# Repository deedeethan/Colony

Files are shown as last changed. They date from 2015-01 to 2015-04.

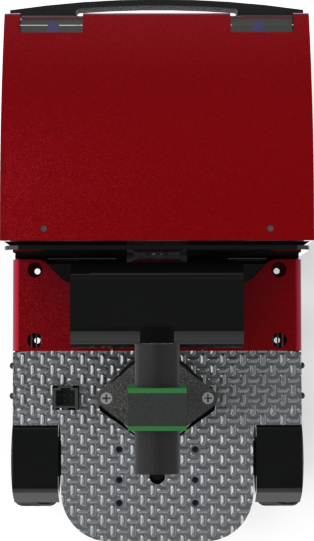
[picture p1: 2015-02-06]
high-level/catkin/misty_working/scoutsim/images/scout_large.png

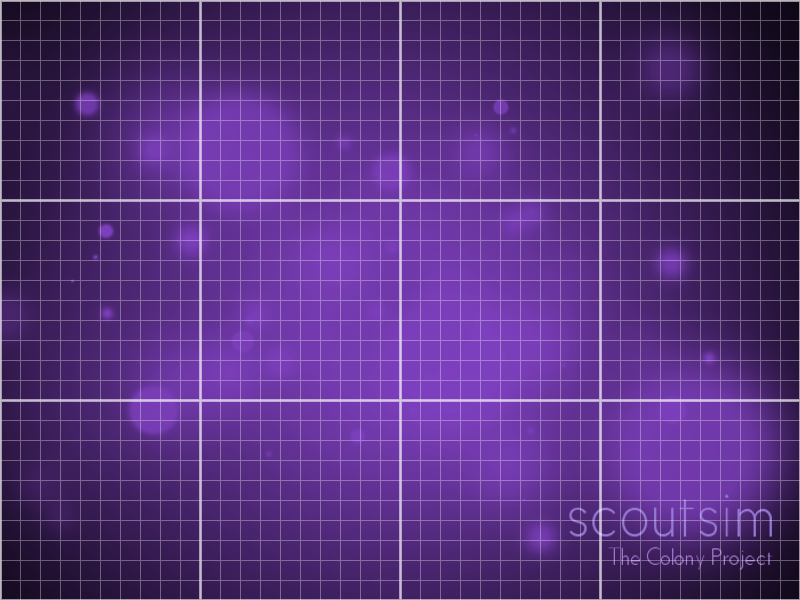
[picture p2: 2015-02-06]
high-level/catkin/misty_working/scoutsim/maps/grid.bmp

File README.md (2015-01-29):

Colony
======

Colony Scout

**General Body Meeting: Thursdays at 5:30pm in WEH 5312**
- Mechanical: Saturdays 1pm in Roboclub
  - contact Jason Dynes (jdynes@andrew.cmu.edu)
- Electrical: Saturdays 1pm in Roboclub
  - contact Jess Chernak (jchernak@andrew.cmu.edu)
- Low Level: Saturdays 3:30pm in Roboclub
  - contact Tom Mullins (tmullins@andrew.cmu.edu)
- High Level: Thursdays after GBM (6:00pm) in WEH 5312
  - contact Tim Brown (twbrown@andrew.cmu.edu)

Contact: [aperley@andrew.cmu.edu](mailto:aperley@andrew.cmu.edu), [jchernak@andrew.cmu.edu](mailto:jchernak@andrew.cmu.edu)

[Wiki](https://github.com/CMU-Robotics-Club/Colony/wiki)
--------------------------------------------------------

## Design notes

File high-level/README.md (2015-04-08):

TODO:
* Catkinize simulator
* Catkinize library/behaviors
* Debug Odometry_new
* Add more colors for each new scout in the simulator
* Remove old track lines when you kill a scout

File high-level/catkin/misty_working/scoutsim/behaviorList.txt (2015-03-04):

pause_scout
danger_marking
draw_ccw_circle
draw_cw_circle
line_follow
maze_solve
maze_solve_simple
navigationMap
Odometry
Odometry_new
Scheduler
smart_runaround
WH_Robot
wl_test

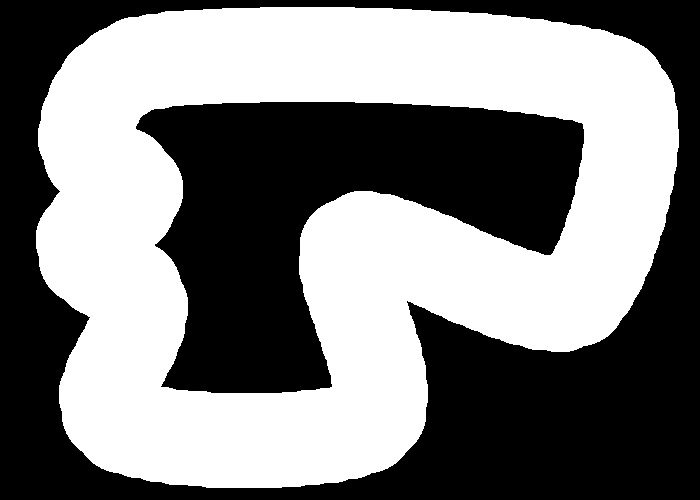
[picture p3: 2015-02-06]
high-level/catkin/misty_working/scoutsim/maps/race_walls.bmp

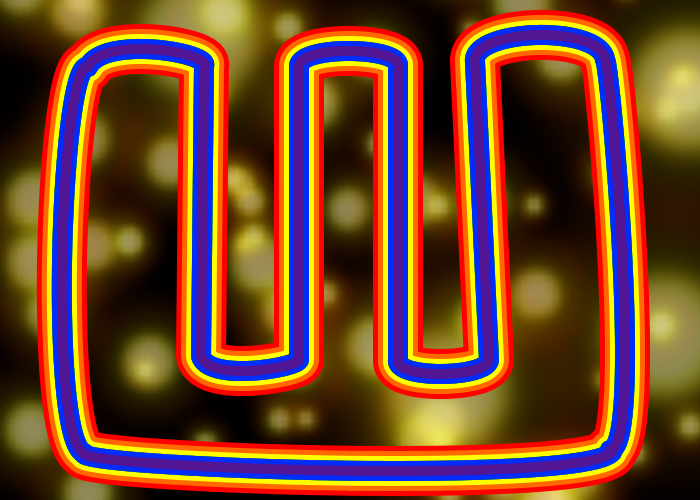
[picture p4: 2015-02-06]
high-level/catkin/misty_working/scoutsim/maps/line_follow3.bmp

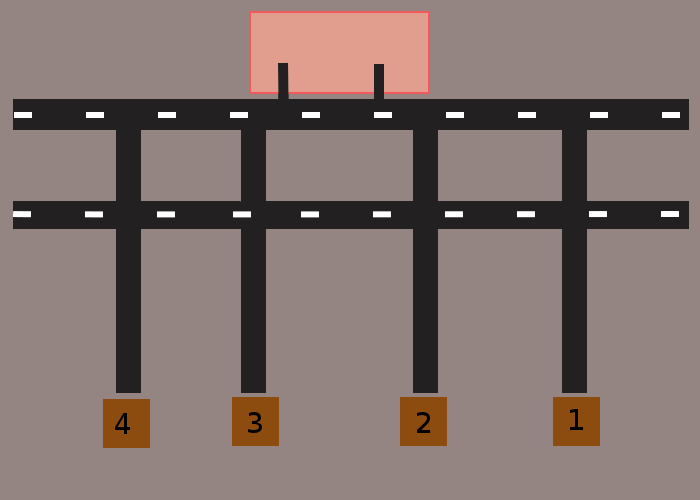
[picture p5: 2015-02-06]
high-level/catkin/misty_working/scoutsim/maps/warehouse.bmp

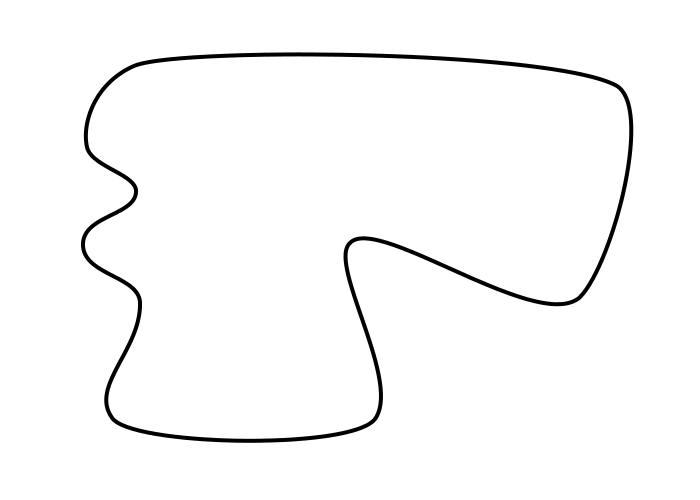
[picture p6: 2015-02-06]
high-level/catkin/misty_working/scoutsim/maps/racetest_lines.bmp

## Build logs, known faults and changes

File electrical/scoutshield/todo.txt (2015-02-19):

ScoutShield
==

- motor controllers
- stepper driver
- IMU
  - accel (MMA8452Q)
  - gyro (L3G4200D)
  - magnometer (MAG3110)
- rgb leds
  - puddle lights
- buttons
  - reset
  - user
  - power switch
- power connector
  - reverse protection
  - fuse
- power indicators
- connectors

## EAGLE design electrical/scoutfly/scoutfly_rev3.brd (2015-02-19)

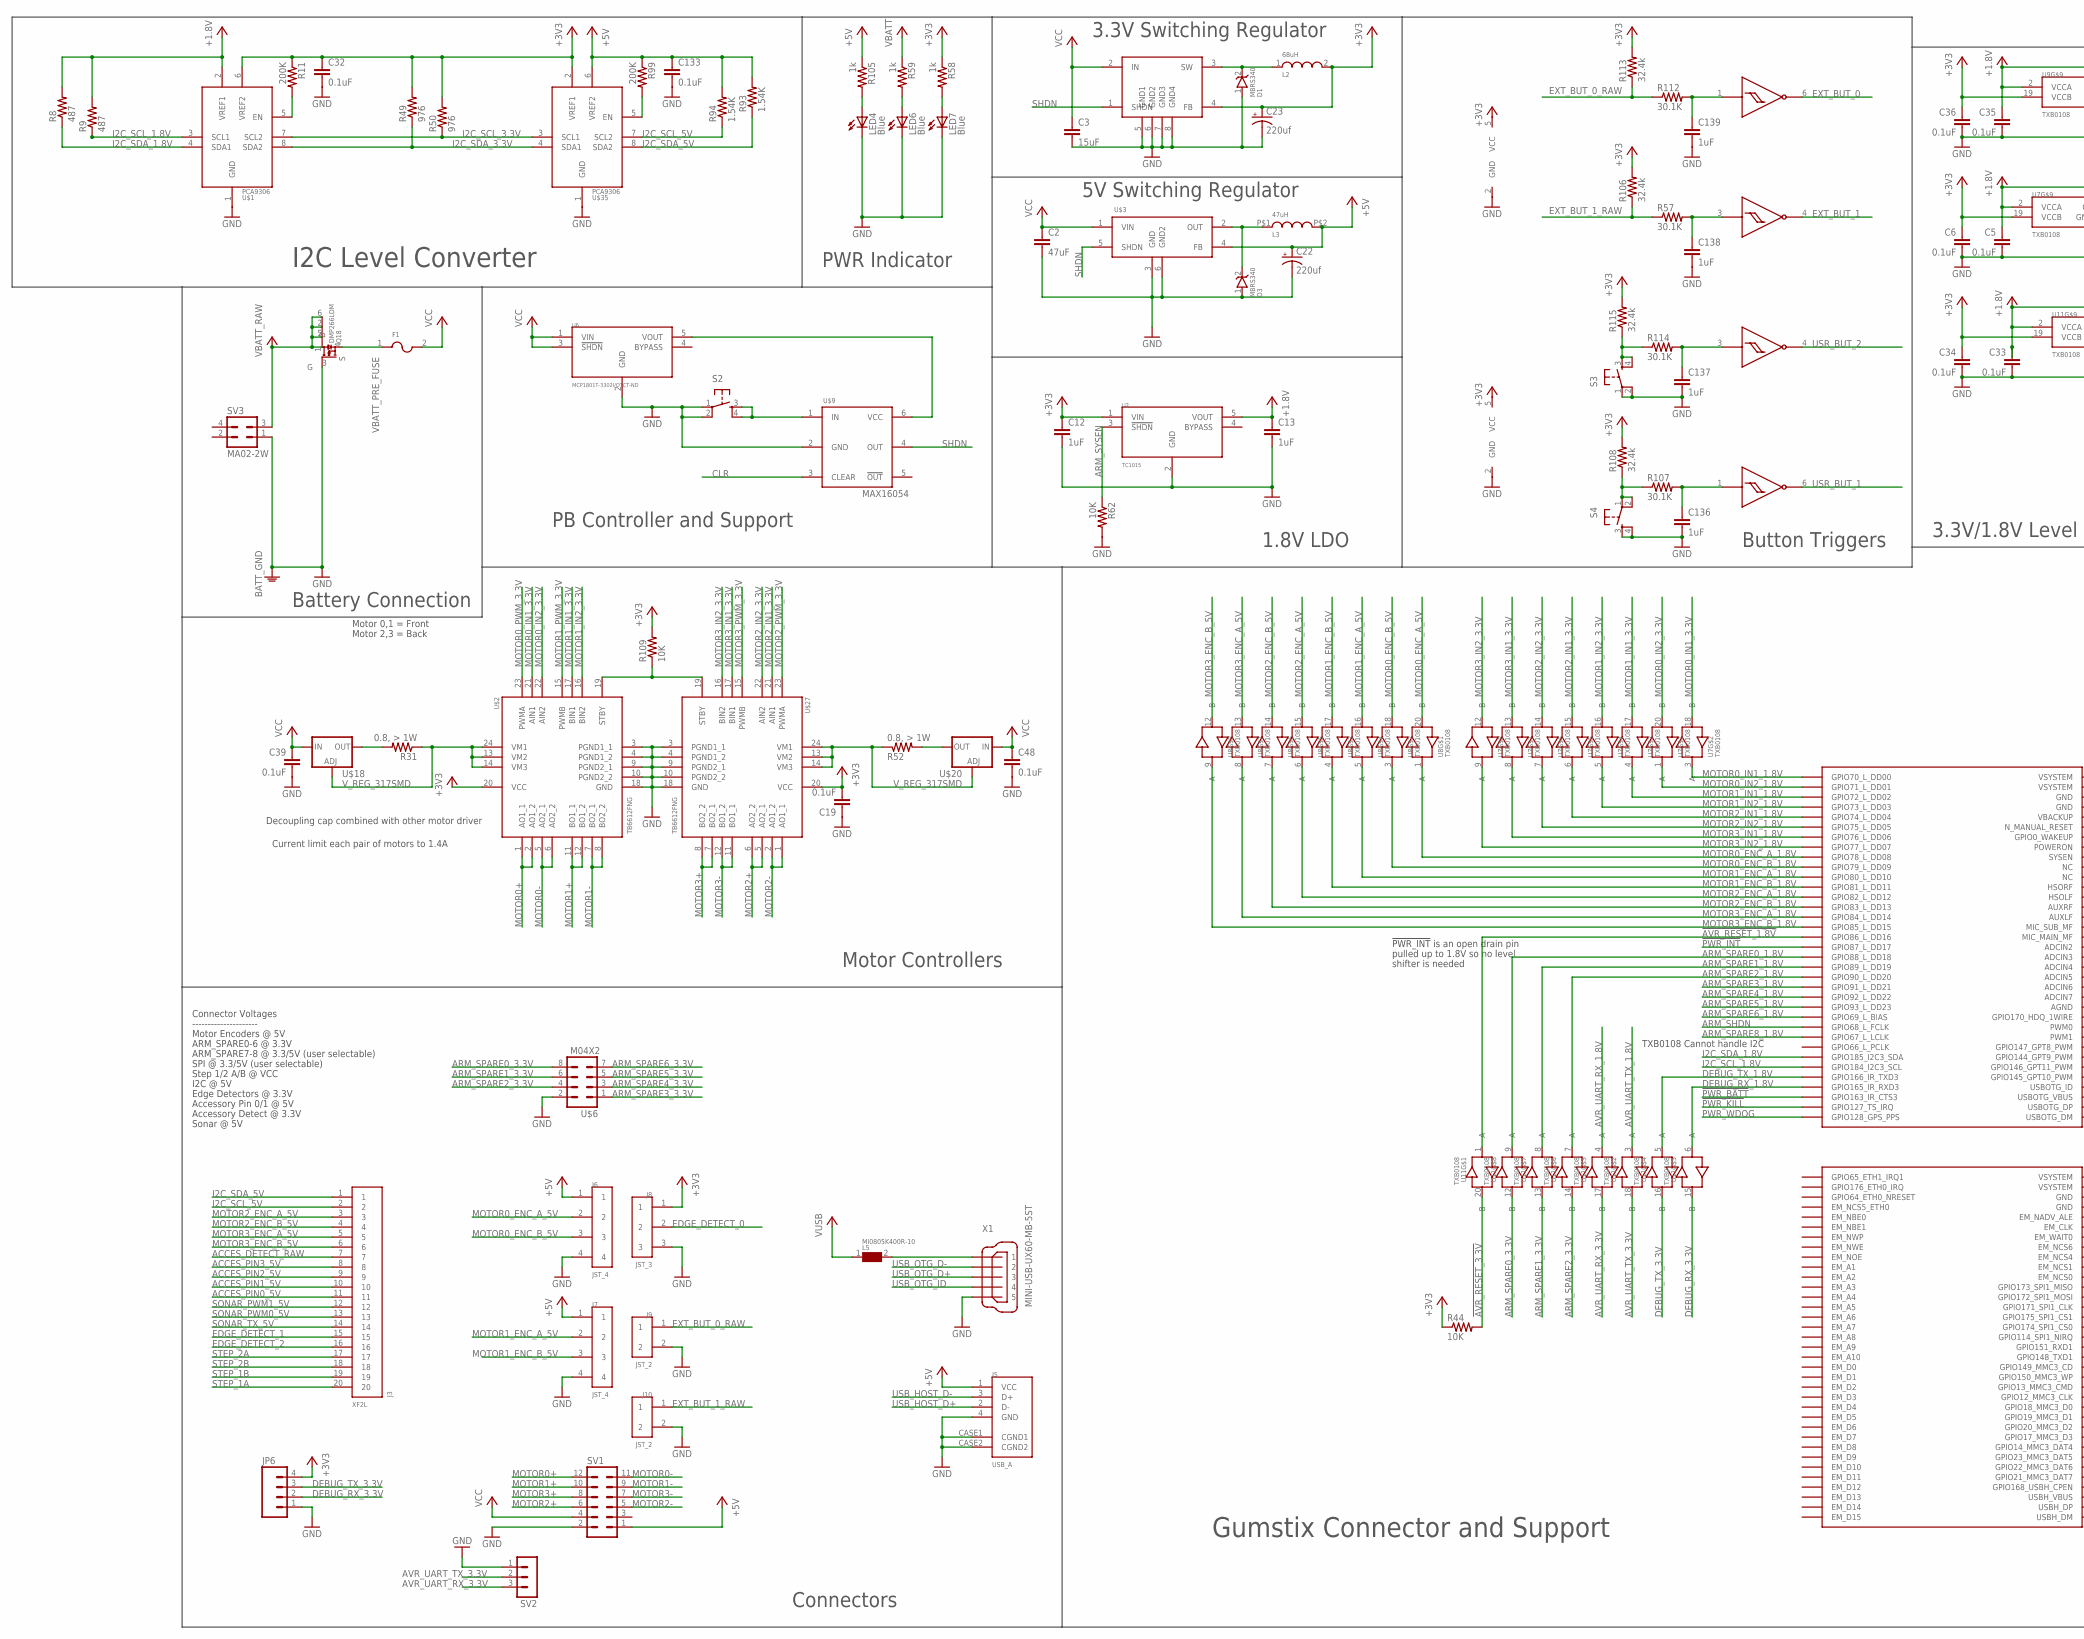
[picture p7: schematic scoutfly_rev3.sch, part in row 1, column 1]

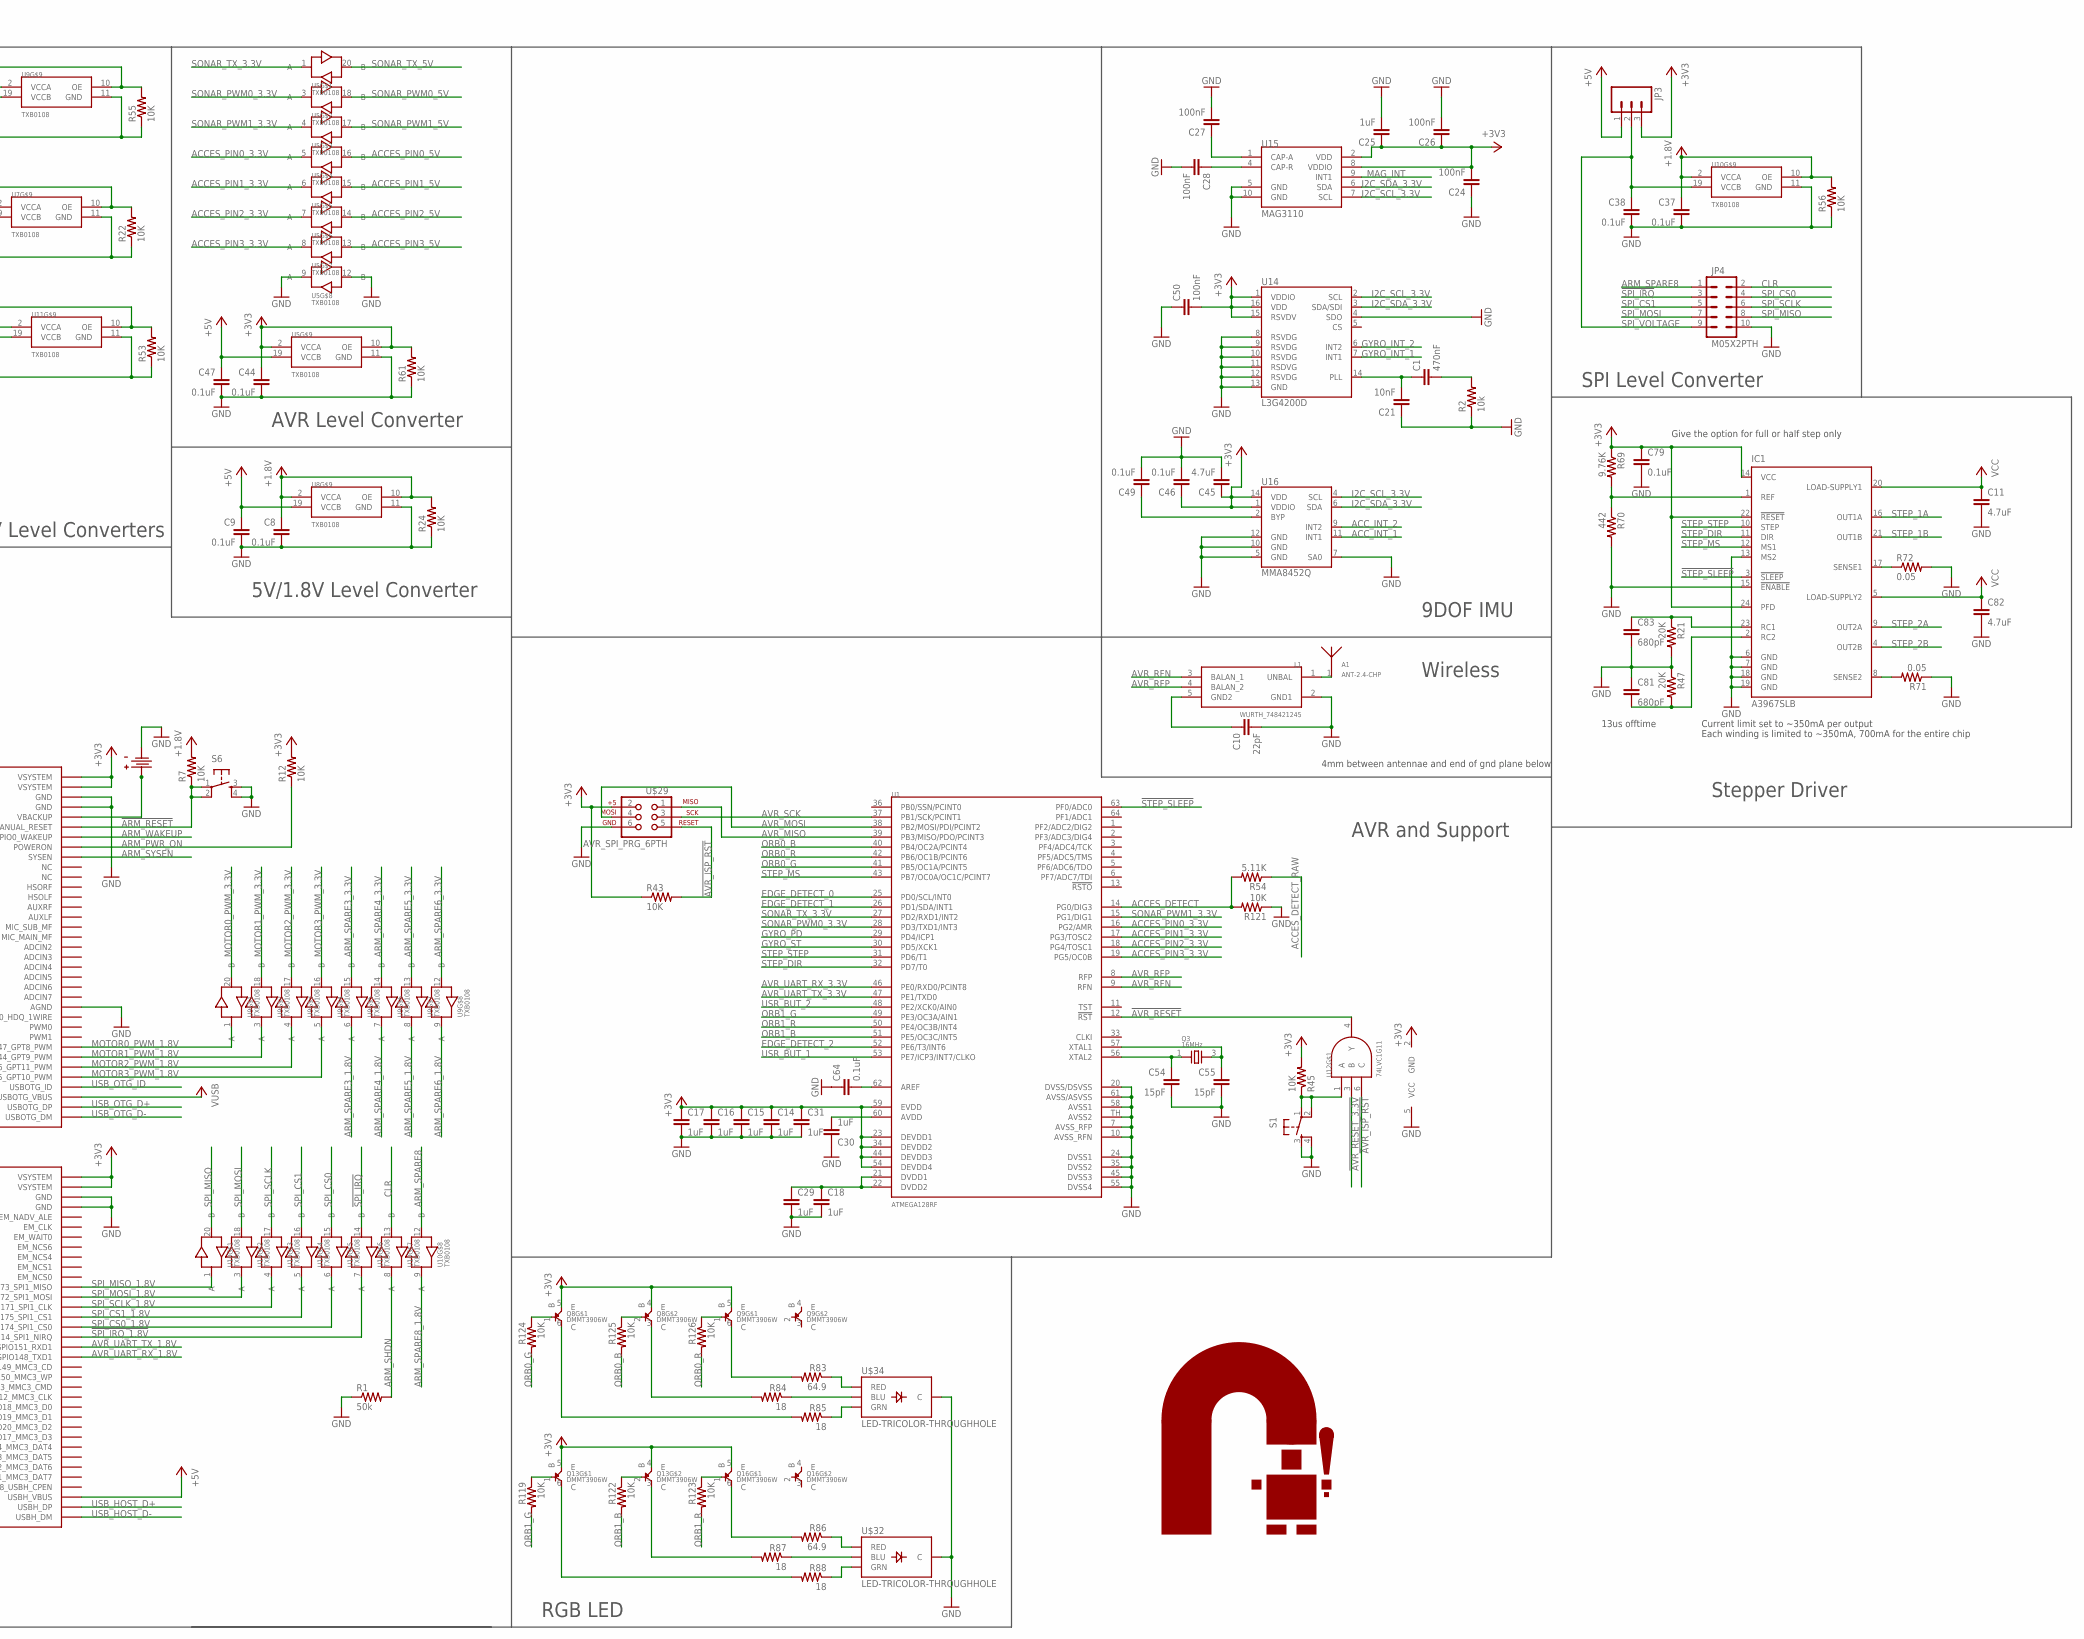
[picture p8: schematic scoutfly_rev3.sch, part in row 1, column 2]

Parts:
A1: ANT-2.4-CHP; CHIP_ANT_2.4GHZ
C1: 470nF; 0603-CAP
C2: 47uF; 0805
C3: 15uF; 0603-CAP
C5, C6, C8, C9, C19, C32, C33, C34, C35, C36, C37, C38, C39, C44, C46, C47, C48, C49, C64, C79, C133: 0.1uF; 0603-CAP
C10: 22pF; 0603-CAP
C11, C82: 4.7uF; C0805
C12, C13, C14, C15, C16, C17, C18, C25, C29, C30, C31, C136, C137, C138, C139: 1uF; 0603-CAP
C21: 10nF; 0603-CAP
C22, C23: 220uf; CT6032
C24, C26, C27, C28, C50: 100nF; 0603-CAP
C45: 4.7uF; 0603-CAP
C54, C55: 15pF; 0603-CAP
C81, C83: 680pF; 0603-CAP
D1, D3: MBRS340; SMC/DO-214AB
F1: MF-SM200; SM200
IC1: A3967SLB; SO24W
J3: XF2L; OMRON_XF
J5: USB_A
J6, J7: JST_4; JST_ZH_4
J8: JST_3; JST_ZH_3
J9, J10: JST_2; JST_ZH_2
J12: KEYSTONE_3000; COIN_CELL
JP3: M03PTH; 1X03
JP4: M05X2PTH; AVR_ICSP
JP6: M04LOCK; 1X04_LOCK
L1: WURTH_748421245; WURTH_BALUN
L2: 68uH; NR6045
L3: 47uH; 0.492L0.492W0.236HINDUCTOR
L5: MI0805K400R-10; 0805
LED4, LED6, LED7: Blue; LED-0603
Q3: 16MHz; NX3225SA
Q8, Q9, Q13, Q16: DMMT3906W; SOT363
Q18: DMP266LDM; SOT26
R1: 50k; R0603
R2: 10k; R0603
R7, R12, R22, R24, R43, R44, R45, R53, R55, R56, R61, R62, R109, R119, R121, R122, R123, R124, R125, R126: 10K; R0603
R8, R9: 487; R0603
R11, R99: 200K; R0603
R21, R47: 20K; R0603
R31, R52: 0.8, > 1W; R2512
R49, R50: 976; R0603
R54: 5.11K; R0603
R57, R107, R112, R114: 30.1K; R0603
R58, R59, R105: 1k; R0603
R69: 9.76K; R0603
R70: 442; R0603
R71, R72: 0.05; R0603
R83, R86: 64.9; R0603
R84, R85, R87, R88: 18; R0603
R93, R94: 1.54K; R0603
R106, R108, R113, R115: 32.4k; R0603
S1, S2, S3, S4, S6: TAC_SWITCHSMD; TACTILE_SWITCH_SMD
SV1: MA06-2W
SV2: MA03-1
SV3: MA02-2W
U1: ATMEGA128RF; MLF64-TH
U2: TC1015; 5-SOT23
U3, U4: NL27WZ14; SOT363
U5, U7, U8, U9, U10, U11: TXB0108; 20-TSSOP
U6: MCP1801T-3302I/OTCT-ND; 5-SOT23
U12: 74LVC1G11; 6-SOT23
U14: L3G4200D; LGA16-4X4
U15: MAG3110; DFN-10
U16: MMA8452Q; QFN-16_0.5MM
U$1, U$35: PCA9306; TSSOP8
U$2, U$27: TB6612FNG; 24-SSOP
U$3: AP1501; DD2PAK
U$6: M04X2; 2X4
U$7: ROBOLOGOSILKSCREEN; RCLOGO
U$9: MAX16054; 6-TSOT23
U$10: MIC4680-3.3YM; 8-SOIC
U$16: OVERO
U$18, U$20: V_REG_317SMD; SOT223
U$29: AVR_SPI_PRG_6PTH; 2X3
U$32, U$34: LED-TRICOLOR-THROUGHHOLE
X1: MINI-USB-UX60-MB-5ST; UX60-MB-5ST

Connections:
!ARM_RESET: R7.1, S6.1, S6.2, U$16.N_MANUAL_RESET
!AVR_ISP_RST: R43.2, U12.6 (C), U$29.5
!AVR_RESET: U1.12 (!RST), U12.4 (Y)
!AVR_RESET_1.8V: U11.1 (A), U$16.GPIO86_L_DD16
!AVR_RESET_3.3V: R44.2, U11.20 (B), U12.3 (B)
!PWR_BATT: U$16.GPIO163_IR_CTS3
!PWR_INT: U$16.GPIO87_L_DD17
!PWR_KILL: U$16.GPIO127_TS_IRQ
!SPI_IRQ: JP4.3, U10.14 (B)
!SPI_IRQ_1.8V: U10.7 (A), U$16.GPIO114_SPI1_NIRQ
!STEP_SLEEP: IC1.3 (!SLEEP), U1.63 (PF0/ADC0)
+1.8V: C5.1, C8.1, C13.1, C33.1, C35.1, C37.1, R7.2, R8.2, R9.2, R22.2, R24.2, R53.2, R55.2, R56.2, U2.5 (VOUT), U7.2 (VCCA), U7.10 (OE), U8.2 (VCCA), U8.10 (OE), U9.2 (VCCA), U9.10 (OE), U10.2 (VCCA), U10.10 (OE), U11.2 (VCCA), U11.10 (OE), U$1.2 (VREF1)
+3V3: C6.1, C12.1, C14.1, C15.1, C16.1, C17.1, C19.2, C23.+, C24.2, C25.1, C26.1, C31.1, C32.1, C34.1, C36.1, C44.1, C45.1, C46.1, C50.2, C79.1, IC1.14 (VCC), IC1.22 (!RESET), IC1.24 (PFD), J8.1, JP3.3, JP6.4, L2.2, Q8.4 (E), Q8.5 (E), Q9.5 (E), Q13.4 (E), Q13.5 (E), Q16.5 (E), R11.1, R12.2, R43.1, R44.1, R45.2, R49.2, R50.2, R58.1, R61.2, R69.1, R106.2, R108.2, R109.2, R113.2, R115.2, U1.23 (DEVDD1), U1.34 (DEVDD2), U1.44 (DEVDD3), U1.54 (DEVDD4), U1.59 (EVDD), U2.1 (VIN), U3.5 (VCC), U4.5 (VCC), U5.2 (VCCA), U5.10 (OE), U7.19 (VCCB), U9.19 (VCCB), U11.19 (VCCB), U12.2 (GND), U14.1 (VDDIO), U14.15 (RSVDV), U14.16 (VDD), U15.2 (VDD), U15.8 (VDDIO), U16.1 (VDDIO), U16.14 (VDD), U$1.6 (VREF2), U$2.20 (VCC), U$10.4 (FB), U$16.VSYSTEM@1 (VSYSTEM), U$16.VSYSTEM@2 (VSYSTEM), U$16.VSYSTEM@66 (VSYSTEM), U$16.VSYSTEM@67 (VSYSTEM), U$27.20 (VCC), U$29.2, U$35.2 (VREF1)
+5V: C9.1, C22.+, C47.1, C133.1, J5.1 (VCC), J6.1, J7.1, JP3.1, L3.P$2 (2), R93.2, R94.2, R99.1, R105.1, SV1.1, U5.19 (VCCB), U8.19 (VCCB), U$3.4 (FB), U$16.USBH_VBUS, U$35.6 (VREF2)
ACCES_DETECT: R54.2, R121.2, U1.14 (PG0/DIG3)
ACCES_DETECT_RAW: J3.7, R54.1
ACCES_PIN0_3.3V: U1.16 (PG2/AMR), U5.5 (A)
ACCES_PIN0_5V: J3.11, U5.16 (B)
ACCES_PIN1_3.3V: U1.17 (PG3/TOSC2), U5.6 (A)
ACCES_PIN1_5V: J3.10, U5.15 (B)
ACCES_PIN2_3.3V: U1.18 (PG4/TOSC1), U5.7 (A)
ACCES_PIN2_5V: J3.9, U5.14 (B)
ACCES_PIN3_3.3V: U1.19 (PG5/OC0B), U5.8 (A)
ACCES_PIN3_5V: J3.8, U5.13 (B)
ACC_INT_1: U16.11 (INT1)
ACC_INT_2: U16.9 (INT2)
ARM_PWR_ON: R12.1, U$16.POWERON
ARM_SHDN: R1.2, U10.8 (A), U$16.GPIO68_L_FCLK
ARM_SPARE0_1.8V: U11.9 (A), U$16.GPIO88_L_DD18
ARM_SPARE0_3.3V: U11.12 (B), U$6.8
ARM_SPARE1_1.8V: U11.8 (A), U$16.GPIO89_L_DD19
ARM_SPARE1_3.3V: U11.13 (B), U$6.6
ARM_SPARE2_1.8V: U11.7 (A), U$16.GPIO90_L_DD20
ARM_SPARE2_3.3V: U11.14 (B), U$6.4
ARM_SPARE3_1.8V: U9.6 (A), U$16.GPIO91_L_DD21
ARM_SPARE3_3.3V: U9.15 (B), U$6.1
ARM_SPARE4_1.8V: U9.7 (A), U$16.GPIO92_L_DD22
ARM_SPARE4_3.3V: U9.14 (B), U$6.3
ARM_SPARE5_1.8V: U9.8 (A), U$16.GPIO93_L_DD23
ARM_SPARE5_3.3V: U9.13 (B), U$6.5
ARM_SPARE6_1.8V: U9.9 (A), U$16.GPIO69_L_BIAS
ARM_SPARE6_3.3V: U9.12 (B), U$6.7
ARM_SPARE8: JP4.1, U10.12 (B)
ARM_SPARE8_1.8V: U10.9 (A), U$16.GPIO67_L_LCLK
ARM_SYSEN: R62.1, U2.3 (!SHDN), U$16.SYSEN
ARM_WAKEUP: U$16.GPIO0_WAKEUP
AVR_MISO: U1.39 (PB3/MISO/PDO/PCINT3), U$29.1
AVR_MOSI: U1.38 (PB2/MOSI/PDI/PCINT2), U$29.4
AVR_RFN: L1.3 (BALAN_1), U1.9 (RFN)
AVR_RFP: L1.4 (BALAN_2), U1.8 (RFP)
AVR_SCK: U1.37 (PB1/SCK/PCINT1), U$29.3
AVR_UART_RX_1.8V: U11.4 (A), U$16.GPIO148_TXD1
AVR_UART_RX_3.3V: SV2.3, U1.46 (PE0/RXD0/PCINT8), U11.17 (B)
AVR_UART_TX_1.8V: U11.3 (A), U$16.GPIO151_RXD1
AVR_UART_TX_3.3V: SV2.2, U1.47 (PE1/TXD0), U11.18 (B)
CLR: JP4.2, U10.13 (B), U$9.3 (CLEAR)
DEBUG_RX_1.8V: U11.6 (A), U$16.GPIO165_IR_RXD3
DEBUG_RX_3.3V: JP6.2, U11.15 (B)
DEBUG_TX_1.8V: U11.5 (A), U$16.GPIO166_IR_TXD3
DEBUG_TX_3.3V: JP6.3, U11.16 (B)
EDGE_DETECT_0: J8.2, U1.25 (PD0/SCL/INT0)
EDGE_DETECT_1: J3.15, U1.26 (PD1/SDA/INT1)
EDGE_DETECT_2: J3.16, U1.52 (PE6/T3/INT6)
EXT_BUT_0: U3.6 (Y)
EXT_BUT_0_RAW: J9.1, R112.1, R113.1
EXT_BUT_1: U3.4 (Y)
EXT_BUT_1_RAW: J10.1, R57.1, R106.1
GND: C2.2, C3.2, C5.2, C6.2, C8.2, C9.2, C10.2, C11.2, C12.2, C13.2, C14.2, C15.2, C16.2, C17.2, C18.2, C19.1, C21.1, C22.-, C23.-, C24.1, C25.2, C26.2, C27.2, C28.2, C29.2, C30.1, C31.2, C32.2, C33.2, C34.2, C35.2, C36.2, C37.2, C38.2, C39.2, C44.2, C45.2, C46.2, C47.2, C48.2, C49.2, C50.1, C54.2, C55.2, C64.1, C79.2, C81.1, C82.2, C83.2, C133.2, C136.2, C137.2, C138.2, C139.2, D1.1, D3.1, IC1.6 (GND), IC1.7 (GND), IC1.13 (MS2), IC1.15 (!ENABLE), IC1.18 (GND), IC1.19 (GND), J5.4 (GND), J5.CASE1 (CGND1), J5.CASE2 (CGND2), J6.4, J7.4, J8.3, J9.2, J10.2, J12.NEGATIVE (-), JP4.10, JP6.1, L1.2 (GND1), LED4.C, LED6.C, LED7.C, Q18.3 (G), R1.1, R2.1, R21.2, R22.1, R24.1, R47.1, R53.1, R55.1, R56.1, R61.1, R62.2, R70.2, R71.1, R72.2, R121.1, S1.3, S1.4, S2.1, S2.2, S3.1, S3.2, S4.3, S4.4, S6.3, S6.4, SV1.2, SV2.1, SV3.1, U1.7 (AVSS_RFP), U1.10 (AVSS_RFN), U1.20 (DVSS/DSVSS), U1.24 (DVSS1), U1.35 (DVSS2), U1.45 (DVSS3), U1.55 (DVSS4), U1.58 (AVSS1), U1.61 (AVSS/ASVSS), U1.TH (AVSS2), U2.2 (GND), U3.2 (GND), U4.2 (GND), U5.9 (A), U5.11 (GND), U5.12 (B), U6.2 (GND), U7.11 (GND), U8.11 (GND), U9.11 (GND), U10.11 (GND), U11.11 (GND), U12.5 (VCC), U14.4 (SDO), U14.8 (RSVDG), U14.9 (RSVDG), U14.10 (RSVDG), U14.11 (RSDVG), U14.12 (RSVDG), U14.13 (GND), U15.5 (GND), U15.10 (GND), U16.5 (GND), U16.7 (SA0), U16.10 (GND), U16.12 (GND), U$1.1 (GND), U$2.3 (PGND1_1), U$2.4 (PGND1_2), U$2.9 (PGND2_1), U$2.10 (PGND2_2), U$2.18 (GND), U$3.3 (GND), U$3.6 (GND2), U$6.2, U$9.2 (GND), U$10.5 (GND1), U$10.6 (GND2), U$10.7 (GND3), U$10.8 (GND4), U$16.AGND, U$16.GND, U$16.GND@33 (GND), U$16.GND@56 (GND), U$16.GND@70 (GND), U$27.3 (PGND1_1), U$27.4 (PGND1_2), U$27.9 (PGND2_1), U$27.10 (PGND2_2), U$27.18 (GND), U$29.6, U$32.GND (C), U$34.GND (C), U$35.1 (GND), X1.5
GYRO_INT_1: U14.7 (INT1)
GYRO_INT_2: U14.6 (INT2)
GYRO_PD: U1.29 (PD4/ICP1)
GYRO_ST: U1.30 (PD5/XCK1)
I2C_SCL_1.8V: R9.1, U$1.3 (SCL1), U$16.GPIO184_I2C3_SCL
I2C_SCL_3.3V: R50.1, U14.2 (SCL), U15.7 (SCL), U16.4 (SCL), U$1.7 (SCL2), U$35.3 (SCL1)
I2C_SCL_5V: J3.2, R94.1, U$35.7 (SCL2)
I2C_SDA_1.8V: R8.1, U$1.4 (SDA1), U$16.GPIO185_I2C3_SDA
I2C_SDA_3.3V: R49.1, U14.3 (SDA/SDI), U15.6 (SDA), U16.6 (SDA), U$1.8 (SDA2), U$35.4 (SDA1)
I2C_SDA_5V: J3.1, R93.1, U$35.8 (SDA2)
MAG_INT: U15.9 (INT1)
MOTOR0+: SV1.12, U$2.1 (AO1_1), U$2.2 (AO1_2)
MOTOR0-: SV1.11, U$2.5 (AO2_1), U$2.6 (AO2_2)
MOTOR0_ENC_A_1.8V: U8.1 (A), U$16.GPIO78_L_DD08
MOTOR0_ENC_A_5V: J6.2, U8.20 (B)
MOTOR0_ENC_B_1.8V: U8.3 (A), U$16.GPIO79_L_DD09
MOTOR0_ENC_B_5V: J6.3, U8.18 (B)
MOTOR0_IN1_1.8V: U7.3 (A), U$16.GPIO70_L_DD00
MOTOR0_IN1_3.3V: U7.18 (B), U$2.21 (AIN1)
MOTOR0_IN2_1.8V: U7.1 (A), U$16.GPIO71_L_DD01
MOTOR0_IN2_3.3V: U7.20 (B), U$2.22 (AIN2)
MOTOR0_PWM_1.8V: U9.1 (A), U$16.GPIO147_GPT8_PWM
MOTOR0_PWM_3.3V: U9.20 (B), U$2.23 (PWMA)
MOTOR1+: SV1.10, U$2.11 (BO1_1), U$2.12 (BO1_2)
MOTOR1-: SV1.9, U$2.7 (BO2_1), U$2.8 (BO2_2)
MOTOR1_ENC_A_1.8V: U8.5 (A), U$16.GPIO80_L_DD10
MOTOR1_ENC_A_5V: J7.2, U8.16 (B)
MOTOR1_ENC_B_1.8V: U8.4 (A), U$16.GPIO81_L_DD11
MOTOR1_ENC_B_5V: J7.3, U8.17 (B)
MOTOR1_IN1_1.8V: U7.4 (A), U$16.GPIO72_L_DD02
MOTOR1_IN1_3.3V: U7.17 (B), U$2.17 (BIN1)
MOTOR1_IN2_1.8V: U7.5 (A), U$16.GPIO73_L_DD03
MOTOR1_IN2_3.3V: U7.16 (B), U$2.16 (BIN2)
MOTOR1_PWM_1.8V: U9.3 (A), U$16.GPIO144_GPT9_PWM
MOTOR1_PWM_3.3V: U9.18 (B), U$2.15 (PWMB)
MOTOR2+: SV1.6, U$27.5 (AO2_1), U$27.6 (AO2_2)
MOTOR2-: SV1.5, U$27.1 (AO1_1), U$27.2 (AO1_2)
MOTOR2_ENC_A_1.8V: U8.6 (A), U$16.GPIO82_L_DD12
MOTOR2_ENC_A_5V: J3.3, U8.15 (B)
MOTOR2_ENC_B_1.8V: U8.7 (A), U$16.GPIO83_L_DD13
MOTOR2_ENC_B_5V: J3.4, U8.14 (B)
MOTOR2_IN1_1.8V: U7.6 (A), U$16.GPIO74_L_DD04
MOTOR2_IN1_3.3V: U7.15 (B), U$27.21 (AIN1)
MOTOR2_IN2_1.8V: U7.7 (A), U$16.GPIO75_L_DD05
MOTOR2_IN2_3.3V: U7.14 (B), U$27.22 (AIN2)
MOTOR2_PWM_1.8V: U9.4 (A), U$16.GPIO146_GPT11_PWM
MOTOR2_PWM_3.3V: U9.17 (B), U$27.23 (PWMA)
MOTOR3+: SV1.8, U$27.7 (BO2_1), U$27.8 (BO2_2)
MOTOR3-: SV1.7, U$27.11 (BO1_1), U$27.12 (BO1_2)
MOTOR3_ENC_A_1.8V: U8.8 (A), U$16.GPIO84_L_DD14
MOTOR3_ENC_A_5V: J3.5, U8.13 (B)
MOTOR3_ENC_B_1.8V: U8.9 (A), U$16.GPIO85_L_DD15
MOTOR3_ENC_B_5V: J3.6, U8.12 (B)
MOTOR3_IN1_1.8V: U7.8 (A), U$16.GPIO76_L_DD06
MOTOR3_IN1_3.3V: U7.13 (B), U$27.17 (BIN1)
MOTOR3_IN2_1.8V: U7.9 (A), U$16.GPIO77_L_DD07
MOTOR3_IN2_3.3V: U7.12 (B), U$27.16 (BIN2)
MOTOR3_PWM_1.8V: U9.5 (A), U$16.GPIO145_GPT10_PWM
MOTOR3_PWM_3.3V: U9.16 (B), U$27.15 (PWMB)
unnamed: A1.1, L1.1 (UNBAL)
unnamed: R45.1, S1.1, S1.2, U12.1 (A)
unnamed: J12.PLUS1 (+), J12.PLUS2 (+2), U$16.VBACKUP
unnamed: C83.1, IC1.23 (RC1), R21.1
unnamed: IC1.17 (SENSE1), R72.1
unnamed: IC1.8 (SENSE2), R71.2
unnamed: C81.2, IC1.2 (RC2), R47.2
unnamed: C10.1, L1.5 (GND2)
unnamed: Q8.1 (B), R124.1
unnamed: D1.2, L2.1, U$10.3 (SW)
unnamed: C30.2, U1.60 (AVDD)
unnamed: D3.2, L3.P$1 (1), U$3.2 (OUT)
unnamed: C18.1, C29.1, U1.21 (DVDD1), U1.22 (DVDD2)
unnamed: R11.2, U$1.5 (EN)
unnamed: C64.2, U1.62 (AREF)
unnamed: R31.1, U$2.13 (VM2), U$2.14 (VM3), U$2.24 (VM1), U$18.1 (ADJ)
unnamed: R31.2, U$18.2 (OUT)
unnamed: R52.1, U$20.1 (ADJ), U$27.13 (VM2), U$27.14 (VM3), U$27.24 (VM1)
unnamed: R52.2, U$20.2 (OUT)
unnamed: C1.1, C21.2, U14.14 (PLL)
unnamed: C1.2, R2.2
unnamed: Q8.2 (B), R125.1
unnamed: Q9.1 (B), R126.1
unnamed: Q16.1 (B), R123.1
unnamed: Q13.2 (B), R122.1
unnamed: Q13.1 (B), R119.1
unnamed: S2.3, S2.4, U$9.1 (IN)
unnamed: U6.5 (VOUT), U$9.6 (VCC)
unnamed: R85.1, U$34.GRN
unnamed: C49.1, U16.2 (BYP)
unnamed: C27.1, U15.1 (CAP-A)
unnamed: C28.1, U15.4 (CAP-R)
unnamed: L5.2, X1.1
unnamed: C55.1, Q3.3 (2), U1.57 (XTAL1)
unnamed: C54.1, Q3.1, U1.56 (XTAL2)
unnamed: C138.1, R57.2, U3.3 (X)
unnamed: IC1.1 (REF), R69.2, R70.1
unnamed: R109.1, U$2.19 (STBY), U$27.19 (STBY)
unnamed: R84.1, U$34.BLU
unnamed: R83.1, U$34.RED
unnamed: Q9.6 (C), R83.2
unnamed: Q8.3 (C), R84.2
unnamed: Q8.6 (C), R85.2
unnamed: R88.1, U$32.GRN
unnamed: R87.1, U$32.BLU
unnamed: R86.1, U$32.RED
unnamed: Q16.6 (C), R86.2
unnamed: Q13.3 (C), R87.2
unnamed: Q13.6 (C), R88.2
unnamed: R99.2, U$35.5 (EN)
unnamed: LED4.A, R105.2
unnamed: LED6.A, R59.2
unnamed: LED7.A, R58.2
unnamed: C139.1, R112.2, U3.1 (X)
unnamed: C137.1, R114.2, U4.3 (X)
unnamed: C136.1, R107.2, U4.1 (X)
unnamed: R107.1, R108.1, S4.1, S4.2
unnamed: R114.1, R115.1, S3.3, S3.4
ORB0_B: R125.2, U1.40 (PB4/OC2A/PCINT4)
ORB0_G: R124.2, U1.41 (PB5/OC1A/PCINT5)
ORB0_R: R126.2, U1.42 (PB6/OC1B/PCINT6)
ORB1_B: R122.2, U1.51 (PE5/OC3C/INT5)
ORB1_G: R119.2, U1.49 (PE3/OC3A/AIN1)
ORB1_R: R123.2, U1.50 (PE4/OC3B/INT4)
PWR_WDOG: U$16.GPIO128_GPS_PPS
SHDN: U$3.5 (SHDN), U$9.4 (OUT), U$10.1 (SHDN)
SONAR_PWM0_3.3V: U1.28 (PD3/TXD1/INT3), U5.3 (A)
SONAR_PWM0_5V: J3.13, U5.18 (B)
SONAR_PWM1_3.3V: U1.15 (PG1/DIG1), U5.4 (A)
SONAR_PWM1_5V: J3.12, U5.17 (B)
SONAR_TX_3.3V: U1.27 (PD2/RXD1/INT2), U5.1 (A)
SONAR_TX_5V: J3.14, U5.20 (B)
SPI_CS0: JP4.4, U10.15 (B)
SPI_CS0_1.8V: U10.6 (A), U$16.GPIO174_SPI1_CS0
SPI_CS1: JP4.5, U10.16 (B)
SPI_CS1_1.8V: U10.5 (A), U$16.GPIO175_SPI1_CS1
SPI_MISO: JP4.8, U10.20 (B)
SPI_MISO_1.8V: U10.1 (A), U$16.GPIO173_SPI1_MISO
SPI_MOSI: JP4.7, U10.18 (B)
SPI_MOSI_1.8V: U10.3 (A), U$16.GPIO172_SPI1_MOSI
SPI_SCLK: JP4.6, U10.17 (B)
SPI_SCLK_1.8V: U10.4 (A), U$16.GPIO171_SPI1_CLK
SPI_VOLTAGE: C38.1, JP3.2, JP4.9, U10.19 (VCCB)
STEP_1A: IC1.16 (OUT1A), J3.20
STEP_1B: IC1.21 (OUT1B), J3.19
STEP_2A: IC1.9 (OUT2A), J3.17
STEP_2B: IC1.4 (OUT2B), J3.18
STEP_DIR: IC1.11 (DIR), U1.32 (PD7/T0)
STEP_MS: IC1.12 (MS1), U1.43 (PB7/OC0A/OC1C/PCINT7)
STEP_STEP: IC1.10 (STEP), U1.31 (PD6/T1)
USB_HOST_D+: J5.2 (D-), U$16.USBH_DP
USB_HOST_D-: J5.3 (D+), U$16.USBH_DM
USB_OTG_D+: U$16.USBOTG_DP, X1.3
USB_OTG_D-: U$16.USBOTG_DM, X1.2
USB_OTG_ID: U$16.USBOTG_ID, X1.4
USR_BUT_1: U1.53 (PE7/ICP3/INT7/CLKO), U4.6 (Y)
USR_BUT_2: U1.48 (PE2/XCK0/AIN0), U4.4 (Y)
VBATT: R59.1
VBATT_PRE_FUSE: F1.1, Q18.4 (S)
VBATT_RAW: Q18.1 (D), Q18.2 (D2), Q18.5 (D3), Q18.6 (D4), SV3.3
VCC: C2.1, C3.1, C11.1, C39.1, C48.1, C82.1, F1.2, IC1.5 (LOAD-SUPPLY2), IC1.20 (LOAD-SUPPLY1), SV1.4, U6.1 (VIN), U6.3 (!SHDN), U$3.1 (VIN), U$10.2 (IN), U$18.3 (IN), U$20.3 (IN)
VUSB: L5.1, U$16.USBOTG_VBUS

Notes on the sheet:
Decoupling cap combined with other motor driver
!PWR_INT! is an open drain pin
pulled up to 1.8V so no level
shifter is needed
TXB0108 Cannot handle I2C
Motor Encoders @ 5V
Connector Voltages
---------------------
ARM_SPARE0-6 @ 3.3V
ARM_SPARE7-8 @ 3.3/5V (user selectable)
SPI @ 3.3/5V (user selectable)
Step 1/2 A/B @ VCC
I2C @ 5V
Edge Detectors @ 3.3V
Accessory Pin 0/1 @ 5V
Accessory Detect @ 3.3V
Sonar @ 5V
Current limit each pair of motors to 1.4A
Current limit set to ~350mA per output
4mm between antennae and end of gnd plane below
Motor 0,1 = Front
Motor 2,3 = Back
Each winding is limited to ~350mA, 700mA for the entire chip
13us offtime
Give the option for full or half step only
3.3V Switching Regulator
5V Switching Regulator
9DOF IMU
Wireless
AVR Level Converter
SPI Level Converter
Button Triggers
3.3V/1.8V Level Converters
AVR and Support
1.8V LDO
PWR Indicator
5V/1.8V Level Converter
RGB LED
Stepper Driver
Gumstix Connector and Support

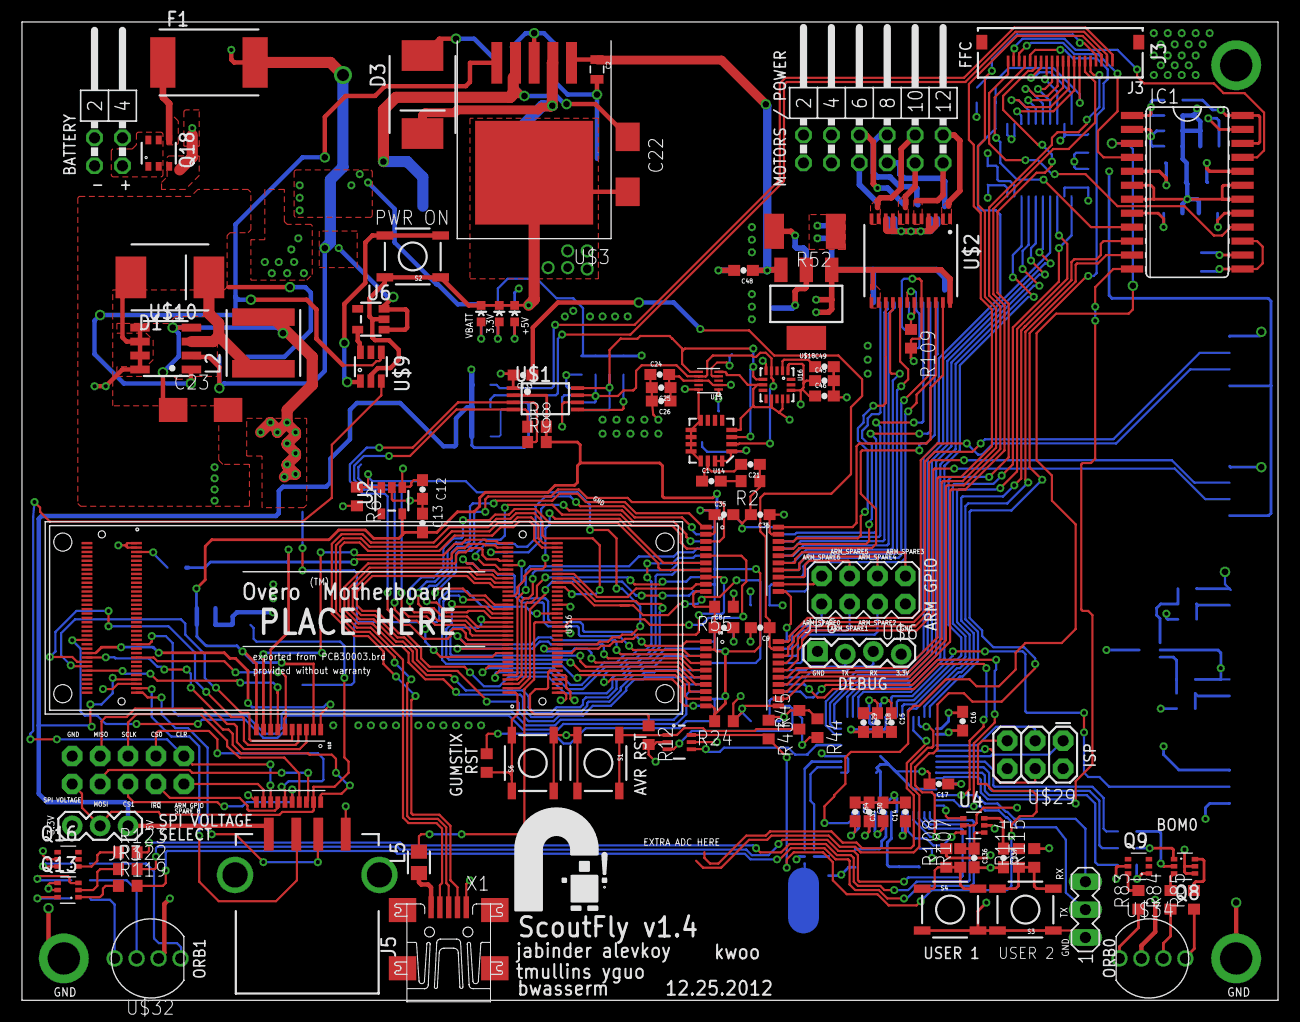
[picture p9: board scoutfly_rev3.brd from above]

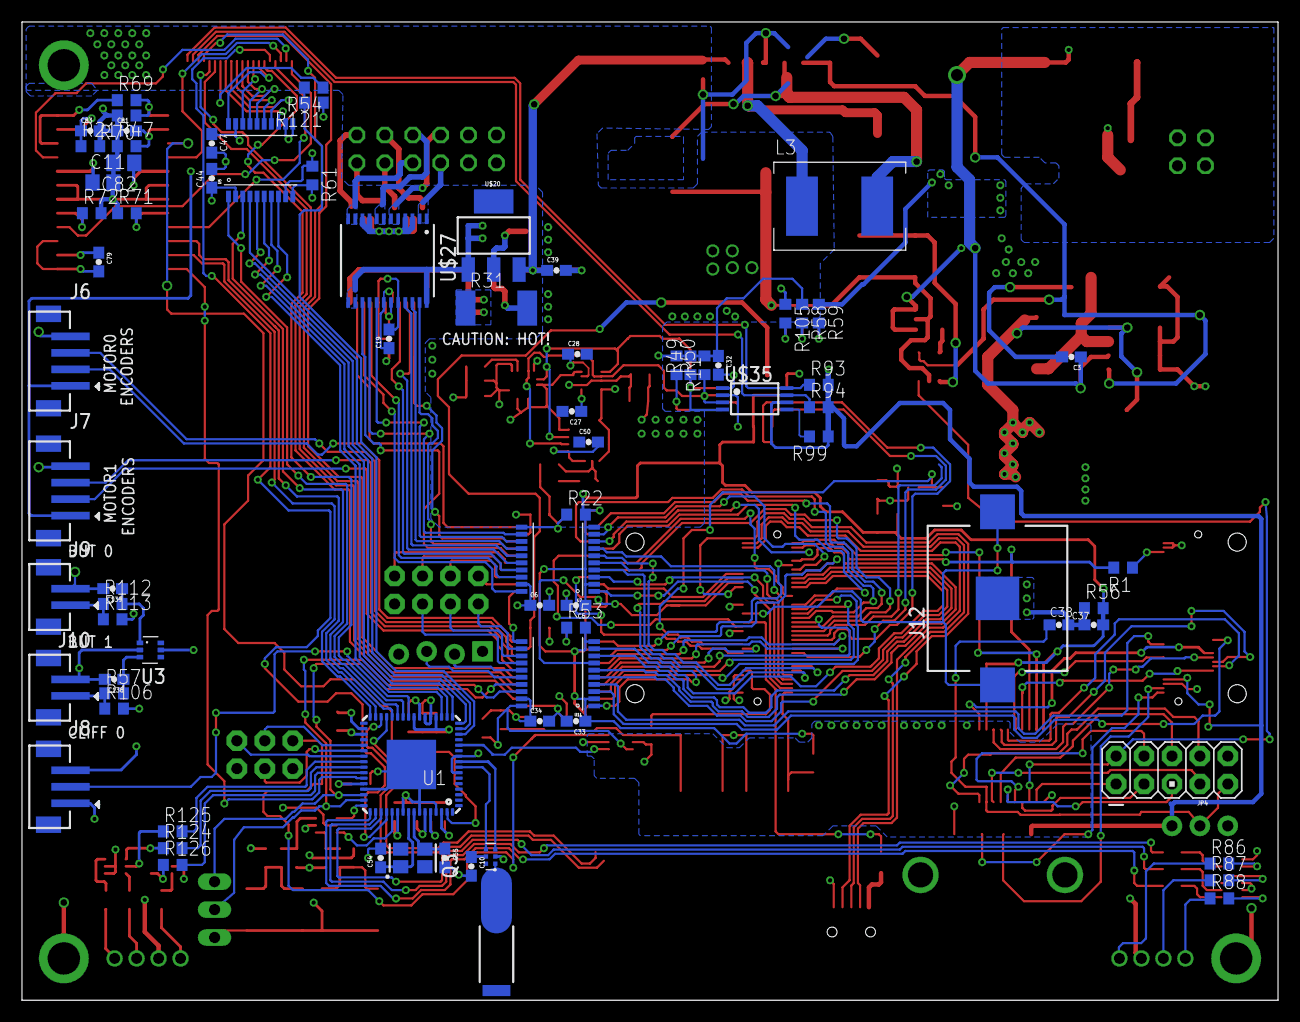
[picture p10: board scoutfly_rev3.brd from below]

Board: 4 copper layers, 114.3 x 89.0 mm, 179 parts (77 on the bottom side), 214 nets.

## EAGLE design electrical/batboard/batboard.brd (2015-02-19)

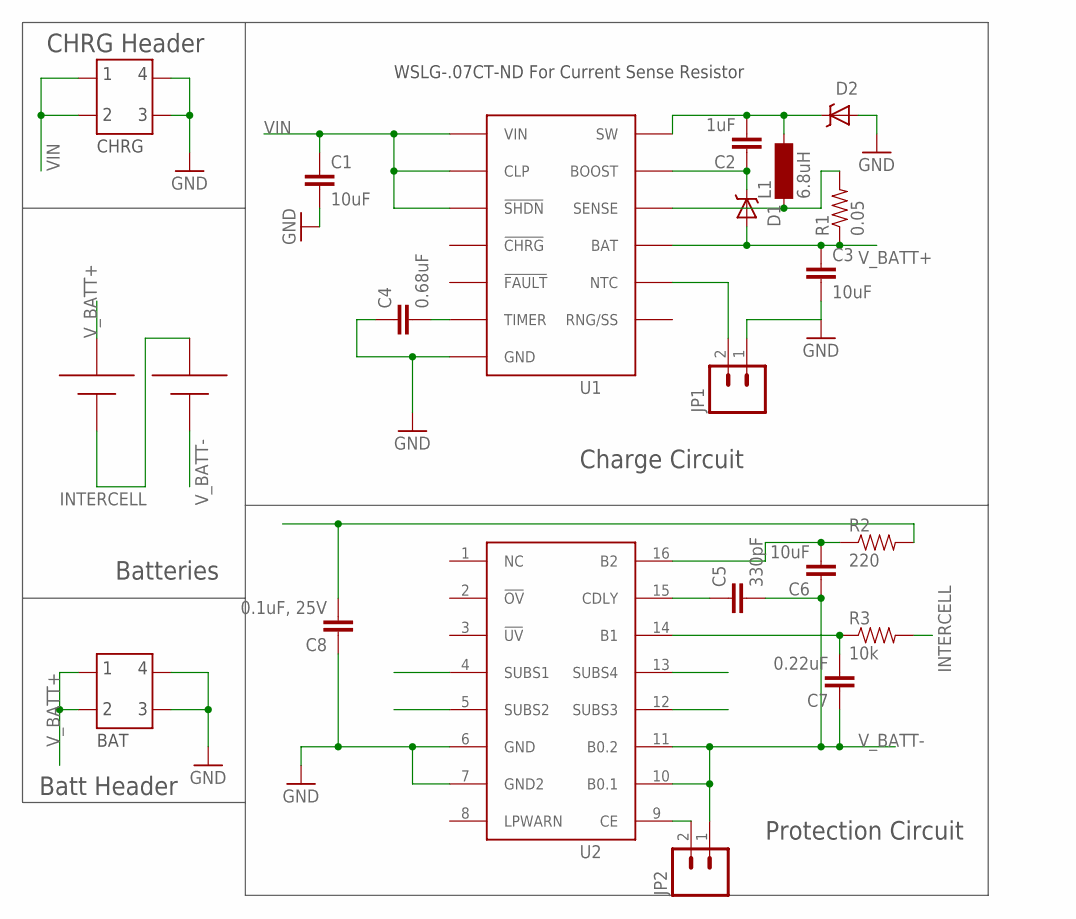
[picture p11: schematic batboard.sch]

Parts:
BAT: C-GRID-71308; 4HEAD_MOLEX_C71308
C1, C3, C6: 10uF; 0805
C2: 1uF; 0805
C4: 0.68uF; 0805
C5: 330pF; 0805
C7: 0.22uF; 0805
C8: 0.1uF, 25V; 0805
CHRG: C-GRID-71308; 4HEAD_MOLEX_C71308
D1, D2: DIODE-SCHOTTKY_; SMA-DIODE
JP1, JP2: M02PTH; 1X02
L1: 6.8uH; SM-1206
R1: 0.05; R2512
R2: 220; 0603-RES
R3: 10k; 0603-RES
U1: LT3650; 12-MSOP
U2: UCC3911; SOIC-16
U$1: BK-18650-PC4; 18650-PC4

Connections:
GND: BAT.3, BAT.4, C1.2, C3.2, C4.1, C8.1, CHRG.3, CHRG.4, D2.A, JP1.1, U1.GND, U2.6 (GND), U2.7 (GND2)
HSINK: U2.4 (SUBS1), U2.5 (SUBS2), U2.12 (SUBS3), U2.13 (SUBS4)
INTERCELL: R3.2, U$1.+2, U$1.-1
unnamed: JP2.2, U2.9 (CE)
unnamed: C2.1, D1.C, U1.11 (BOOST)
unnamed: JP1.2, U1.8 (NTC)
unnamed: C4.2, U1.6 (TIMER)
unnamed: C2.2, D2.C, L1.2, U1.12 (SW)
unnamed: L1.1, R1.2, U1.10 (SENSE)
unnamed: C5.1, U2.15 (CDLY)
unnamed: C6.2, R2.1, U2.16 (B2)
unnamed: C7.2, R3.1, U2.14 (B1)
VIN: C1.1, CHRG.1, CHRG.2, U1.1 (VIN), U1.2 (CLP), U1.3 (!SHDN)
V_BATT+: BAT.1, BAT.2, C3.1, C8.2, D1.A, R1.1, R2.2, U1.9 (BAT), U$1.+1
V_BATT-: C5.2, C6.1, C7.1, JP2.1, U2.10 (B0.1), U2.11 (B0.2), U$1.-2

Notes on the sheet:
Batteries
Batt Header
CHRG Header
WSLG-.07CT-ND For Current Sense Resistor
Charge Circuit
Protection Circuit

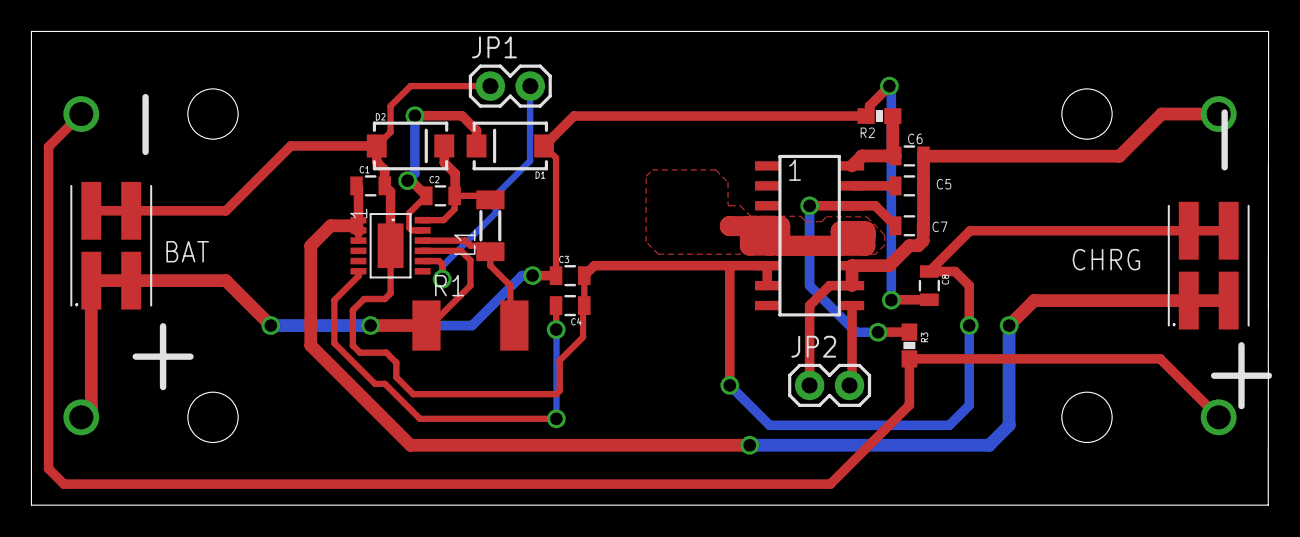
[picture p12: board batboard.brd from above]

Board: 2 copper layers, 78.7 x 30.1 mm, 21 parts (1 on the bottom side), 15 nets.

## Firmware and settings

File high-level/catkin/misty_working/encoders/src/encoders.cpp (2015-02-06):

/**
 * Copyright (c) 2011 Colony Project
 * 
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
 * THE SOFTWARE IS PROVIDED "AS IS", WITHOUT WARRANTY OF ANY KIND,
 * EXPRESS OR IMPLIED, INCLUDING BUT NOT LIMITED TO THE WARRANTIES
 * OF MERCHANTABILITY, FITNESS FOR A PARTICULAR PURPOSE AND
 * NONINFRINGEMENT. IN NO EVENT SHALL THE AUTHORS OR COPYRIGHT
 * HOLDERS BE LIABLE FOR ANY CLAIM, DAMAGES OR OTHER LIABILITY,
 * WHETHER IN AN ACTION OF CONTRACT, TORT OR OTHERWISE, ARISING
 * FROM, OUT OF OR IN CONNECTION WITH THE SOFTWARE OR THE USE OR
 * OTHER DEALINGS IN THE SOFTWARE.
 */

/**
 * @file encoders.cpp
 * @brief Encoders
 *
 * @defgroup encoders Encoders
 * @brief Functions for using the encoders
 *
 * @author Colony Project, CMU Robotics Club
 * @author Alex Zirbel
 * @author Tom Mullins

 * @{
 **/

#include <fstream>
#include <ros/ros.h>
#include "encoders.h"

/* Encoder instances */
/* @todo make sure these are the correct numbers */
static Encoder encoder_fl(0);
static Encoder encoder_fr(1);
static Encoder encoder_bl(2);
static Encoder encoder_br(3);

/**
 * @brief Encoder constructor
 *
 * Opens device file, which is read at every call to get_ticks
 *
 * @param n The encoder number to read, between 0 and 3 inclusive
 */
Encoder::Encoder(int n)
{
    sprintf(filename, "/sys/class/encoder/enc%d/ticks", n);
}

/**
 * @brief Returns the current tick count
 *
 * This will actually read from the encoder ticks file to get the latest value
 * from the driver
 */
int Encoder::get_ticks()
{
    // open device file
    std::fstream fticks(filename, std::ios::in);

    int ticks;
    fticks >> ticks;

    return ticks;
}

/**
 * @brief Resets the encoder
 *
 * Sets the encoder's ticks value back to 0
 */
void Encoder::reset()
{
    std::fstream fticks(filename, std::ios::out);
    fticks << 0;
}

/**
 * @brief Outputs current encoder data
 *
 * Serves the service query_encoders by responding to service requests with the
 * encoder values.
 * @param req The request. The units that the response should be in.
 * @param res The response. The fields will be filled with values.
 */
bool handle_encoders_query(::messages::query_encoders::Request  &req,
                           ::messages::query_encoders::Response &res)
{
    /* Put index, velocity, and distance data in message */
    res.fl_distance = -encoder_fl.get_ticks();
    res.fr_distance = encoder_fr.get_ticks();
    res.bl_distance = encoder_bl.get_ticks();
    res.br_distance = encoder_br.get_ticks();

    /* @todo maybe return value based on whether reads succeeded */

    ROS_DEBUG("Encoder values queried");
    ROS_INFO("Encoder values queried %d  %d  %d   %d", res.fl_distance, res.fr_distance, res.bl_distance, res.br_distance);
    return true;
}

/**
 * @brief Resets all four encoders
 *
 * Serves the service reset_encoders
 * @param req The request. Empty.
 * @param res The response. Empty.
 */
bool handle_reset_query(::messages::reset_encoders::Request &req,
                        ::messages::reset_encoders::Response &res)
{
    encoder_fl.reset();
    encoder_fr.reset();
    encoder_bl.reset();
    encoder_br.reset();
    return true;
}

/**
 * @brief Encoders driver. This is a ROS node that controls encoders.
 *
 * This is the main function for the encoders node. It is run when the node
 * starts and initializes the encoders. It then publishes to the
 * encoder_state topic and advertises the query_encoders service.
 */
int main(int argc, char **argv)
{
    /* Initialize in ROS the encoders driver node */
    ros::init(argc, argv, "encoders_driver");

    /* Advertise that this serves the query_encoders service */
    ros::NodeHandle n;
    ros::ServiceServer service =
        n.advertiseService("query_encoders",
                           handle_encoders_query);

    ROS_INFO("Ready to set encoders.");

    ros::spin();

    return 0;
}

/** @} */

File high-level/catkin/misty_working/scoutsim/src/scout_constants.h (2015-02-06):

/**
 * The code in this package was developed using the structure of Willow
 * Garage's turtlesim package.  It was modified by the CMU Robotics Club
 * to be used as a simulator for the Colony Scout robot.
 *
 * All redistribution of this code is limited to the terms of Willow Garage's
 * licensing terms, as well as under permission from the CMU Robotics Club.
 * 
 * Copyright (c) 2011 Colony Project
 * 
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
 * Copyright (c) 2009, Willow Garage, Inc.
 * All rights reserved.
 * 
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
 *    Redistributions of source code must retain the above copyright
 *       notice, this list of conditions and the following disclaimer.
 *    Redistributions in binary form must reproduce the above copyright
 *       notice, this list of conditions and the following disclaimer in the
 *       documentation and/or other materials provided with the distribution.
 *    Neither the name of the Willow Garage, Inc. nor the names of its
 *       contributors may be used to endorse or promote products derived from
 *       this software without specific prior written permission.
 * 
 * THE SOFTWARE IS PROVIDED "AS IS", WITHOUT WARRANTY OF ANY KIND,
 * EXPRESS OR IMPLIED, INCLUDING BUT NOT LIMITED TO THE WARRANTIES
 * OF MERCHANTABILITY, FITNESS FOR A PARTICULAR PURPOSE AND
 * NONINFRINGEMENT. IN NO EVENT SHALL THE AUTHORS OR COPYRIGHT
 * HOLDERS BE LIABLE FOR ANY CLAIM, DAMAGES OR OTHER LIABILITY,
 * WHETHER IN AN ACTION OF CONTRACT, TORT OR OTHERWISE, ARISING
 * FROM, OUT OF OR IN CONNECTION WITH THE SOFTWARE OR THE USE OR
 * OTHER DEALINGS IN THE SOFTWARE.
 */

/**
 * @file scout_constants.h
 *
 * @ingroup scoutsim
 * @{
 */

#ifndef _SCOUTSIM_SCOUT_CONSTANTS_
#define _SCOUTSIM_SCOUT_CONSTANTS_

#include <messages/set_motors.h>

/// @todo put these in a utility file somewhere?
#define min(x,y) ((x < y) ? x : y)
#define max(x,y) ((x > y) ? x : y)

namespace scoutsim
{
    // Maximum speed which will be sent to scoutsim in absolute units
    const int MAX_ABSOLUTE_SPEED = messages::set_motors::MAX_SPEED;
    const int MIN_ABSOLUTE_SPEED = messages::set_motors::MIN_SPEED;

    // Speed in m/s corresponding to maximum absolute speed
    const float MAX_SPEED_MPS = 1.0;

    // Pixels in scoutsim per real-world meter.
    // Note that scout image size has been set based on this.
    const float PIX_PER_METER = 200.0;

    // Scout dimensions, in meters
    const float SCOUT_WIDTH = 0.125;
    const float SCOUT_LENGTH = 0.23;

    // Position of sonar relative to robot center
    const float SCOUT_SONAR_X = -0.01;
    const float SCOUT_SONAR_Y = 0.0;

    // @todo Inaccurate. Update
    const float ENCODER_TICKS_PER_METER = 363.78;

    // @todo Update this
    const float SONAR_MAX_RANGE_M = 9.144;
    const unsigned int SONAR_MAX_RANGE_PIX = (unsigned int)
        (SONAR_MAX_RANGE_M * PIX_PER_METER);

    // Time it takes for the sonar to spin from position 0 to position 23
    const float SONAR_HALF_SPIN_TIME = 0.5;

    const float REAL_TIME_REFRESH_RATE = 0.05;   // s
    const float SIM_TIME_REFRESH_RATE = 0.02;   // s
}

#endif

/** @} */

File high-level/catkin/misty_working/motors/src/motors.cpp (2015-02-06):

/**
 * Copyright (c) 2011 Colony Project
 * 
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
 * THE SOFTWARE IS PROVIDED "AS IS", WITHOUT WARRANTY OF ANY KIND,
 * EXPRESS OR IMPLIED, INCLUDING BUT NOT LIMITED TO THE WARRANTIES
 * OF MERCHANTABILITY, FITNESS FOR A PARTICULAR PURPOSE AND
 * NONINFRINGEMENT. IN NO EVENT SHALL THE AUTHORS OR COPYRIGHT
 * HOLDERS BE LIABLE FOR ANY CLAIM, DAMAGES OR OTHER LIABILITY,
 * WHETHER IN AN ACTION OF CONTRACT, TORT OR OTHERWISE, ARISING
 * FROM, OUT OF OR IN CONNECTION WITH THE SOFTWARE OR THE USE OR
 * OTHER DEALINGS IN THE SOFTWARE.
 */

/**
 * @file motors.cpp
 * @brief Contains code to control the motors.
 *
 * @defgroup motors Motors
 * @brief Functions for using the motors
 *
 * @author Colony Project, CMU Robotics Club
 * @author Ben Wasserman
 * @author Tom Mullins
 *
 * @{
 */

#include <ros/ros.h>
#include <cstdlib>
#include "motors.h"

using namespace std;

/**
 * @brief Motor constructor
 *
 * Opens device file and reads initial PWM value
 *
 * @param filename The name of the PWM device file
 */
Motor::Motor(int pwm_gpt, int in1_gpio, int in2_gpio)
{
    char buf[60];

    // open device files
    sprintf(buf, "/dev/pwm%d", pwm_gpt);
    fpwm.open(buf, ios::out);
    sprintf(buf, "/sys/class/gpio/gpio%d/value", in1_gpio);
    fin1.open(buf, ios::out);
    sprintf(buf, "/sys/class/gpio/gpio%d/value", in2_gpio);
    fin2.open(buf, ios::out);

    /* I set speed to 0 here rather than reading in what the current speed is
     * because the pwm driver does not support seeking in the device files.
     * Doing both reading and writing causes fpwm to attempt seeking, which
     * fails, causing fpwm to refuse to do any more io. So, we can only write.
     */
    speed = 0;

    // ensure we are in a consistent state by writing to hardware
    set_speed(speed);
}

/**
 * @brief Motor destructor
 *
 * Sets the motor's speed to zero in preparation for the node exiting
 */
Motor::~Motor()
{
    set_speed(0);
}

/**
 * @brief Returns current motor speed
 *
 * Note that this doesn't read from the hardware
 */
int Motor::get_speed()
{
    return speed;
}

/**
 * @brief Sets motor speed
 *
 * This will set the member this->speed and write the new speed to the hardware
 *
 * @param new_speed The speed to set, between +/- MAXSPEED inclusive
 */
void Motor::set_speed(int new_speed)
{
    int pwm, in1, in2;

    speed = new_speed;

    // convert to hardware units
    if (speed == 0)
    {
        /// @todo should this be off (00) or short brake (11)?
        pwm = 0;
        in1 = 0;
        in2 = 0;
    }
    else if (speed > 0)
    {
        // CW
        pwm = speed;
        in1 = 1;
        in2 = 0;
    }
    else
    {
        // CCW
        pwm = -speed;
        in1 = 0;
        in2 = 1;
    }

    // write to hardware
    fpwm << pwm << flush;
    fin1 << in1 << flush;
    fin2 << in2 << flush;
}

/// @todo change these to the correct motor locations / directions
// Motor state variables
static Motor motor_fl( 8, 70, 71);
static Motor motor_fr( 9, 72, 73);
static Motor motor_bl(11, 74, 75);
static Motor motor_br(10, 76, 77);

/**
 * @brief Sets motor speed
 *
 * Sets the motor speeds based on subscription to the set_motors topic.
 *
 * @param msg The message from the set_motors topic, containing speeds and
 *  motor configuration settings.
 */
void motors_set(const ::messages::set_motors::ConstPtr& msg)
{
    if(msg->fl_set)
    {
        motor_fl.set_speed(msg->fl_speed);
    }
    if(msg->fr_set)
    {
        motor_fr.set_speed(msg->fr_speed);
    }
    if(msg->bl_set)
    {
        motor_bl.set_speed(msg->bl_speed);
    }
    if(msg->br_set)
    {
        motor_br.set_speed(msg->br_speed);
    }

    ROS_DEBUG("Motor speeds set");
}

/**
 * @brief Outputs current motor speeds
 *
 * Serves the service query_motors by responding to service requests with the
 * speeds of the motors.
 * @param req The request. The only field is the units requested.
 * @param res The response. The fields will be filled with values.
 */
bool motors_query(::messages::query_motors::Request &req,
                  ::messages::query_motors::Response &res)
{
    res.fl_speed = motor_fl.get_speed();
    res.fr_speed = motor_fr.get_speed();
    res.bl_speed = motor_bl.get_speed();
    res.br_speed = motor_br.get_speed();

    ROS_DEBUG("Motor speeds queried");

    return true;
}

/**
 * @brief Motors driver. This is a ROS node that controls motor speeds.
 *
 * This is the main function for the motors node. It is run when the node
 * starts and initializes the motors. It then subscribes to the
 * set_motors, and set_motor_speeds topics, and advertises the
 * query_motors service.
 * 
 * @param argc The number of command line arguments (should be 1)
 * @param argv The array of command line arguments
 */
int main(int argc, char **argv)
{
    /* Initialize in ROS the motors driver node */
    ros::init(argc, argv, "motors_driver");

    /* Advertise that this serves the query_motors service */
    ros::NodeHandle node;
    ros::ServiceServer service = node.advertiseService("query_motors",
                                                       motors_query);

    /* Subscribe to the set_motors topic */
    ros::Subscriber sub0 = node.subscribe("set_motors", QUEUE_SIZE, motors_set);

    ROS_INFO("Motors node ready.");
    ros::spin();

    return 0;
}

/** @} */

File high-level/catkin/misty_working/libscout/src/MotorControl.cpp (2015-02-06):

/**
 * Copyright (c) 2011 Colony Project
 * 
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
 * THE SOFTWARE IS PROVIDED "AS IS", WITHOUT WARRANTY OF ANY KIND,
 * EXPRESS OR IMPLIED, INCLUDING BUT NOT LIMITED TO THE WARRANTIES
 * OF MERCHANTABILITY, FITNESS FOR A PARTICULAR PURPOSE AND
 * NONINFRINGEMENT. IN NO EVENT SHALL THE AUTHORS OR COPYRIGHT
 * HOLDERS BE LIABLE FOR ANY CLAIM, DAMAGES OR OTHER LIABILITY,
 * WHETHER IN AN ACTION OF CONTRACT, TORT OR OTHERWISE, ARISING
 * FROM, OUT OF OR IN CONNECTION WITH THE SOFTWARE OR THE USE OR
 * OTHER DEALINGS IN THE SOFTWARE.
 */

/**
 * @file MotorControl.cpp
 * @brief Contains motor declarations and functions
 * 
 * @defgroup motorcontrol MotorControl
 * @brief Functions which a behavior can use to control the motors.
 * @ingroup behavior
 *
 * @author Colony Project, CMU Robotics Club
 * @author Ben Wasserman
 * @author Alex Zirbel
 *
 * @{
 **/

#include "MotorControl.h"

using namespace std;

/**
 * @brief Initialize the motors module of libscout.
 *
 * Initialize the libscout node as a publisher of set_motors and a client of
 * query_motors.
 */
MotorControl::MotorControl(const ros::NodeHandle& libscout_node,
                           string scoutname)
    : node(libscout_node)
{
    set_motors_pub =
        node.advertise< ::messages::set_motors>(scoutname + "/set_motors",
                                           QUEUE_SIZE, true);
    query_motors_client =
        node.serviceClient< ::messages::query_motors>(scoutname + "/query_motors");
}

MotorControl::~MotorControl()
{
    set_sides(0, 0, MOTOR_ABSOLUTE);
}

/**
 * @brief Sets all the speeds according to the specificiation of which motors
 *        to set.
 *
 * @param which A bitmask of which motors need to be set.
 * @param speed The value to set the motors to.
 * @param units The units the speed is expressed in.
 * @return Function status
 */
void MotorControl::set(int which, float speed, char units)
{
    float speed_fl, speed_fr, speed_bl, speed_br;
    speed_fl = speed_fr = speed_bl = speed_br = speed;

    if(which & MOTOR_FL_REV)
    {
        speed_fl = -speed;
    }
    if(which & MOTOR_FR_REV)
    {
        speed_fr = -speed;
    }
    if(which & MOTOR_BL_REV)
    {
        speed_bl = -speed;
    }
    if(which & MOTOR_BR_REV)
    {
        speed_br = -speed;
    }

    set_each(which, speed_fl, speed_fr, speed_bl, speed_br, units);
}

/**
 * @brief Sets the left and right sides of scout to different speeds.
 *
 * @param speed_l The speed of both left motors.
 * @param speed_r The speed of both right motors.
 * @param units The units to set to.
 * @return Function status
 */
void MotorControl::set_sides(float speed_l, float speed_r, char units)
{
    set_each(MOTOR_ALL, speed_l, speed_r, speed_l, speed_r, units);
}

/**
 * @brief Set motor speeds
 * Sets the speeds of the motors as a percentage of top speed. Can selectively
 * select which motors to set, and which to keep at previous speed.
 *
 * @param which A bitmask of which motors should be set.
 * @param speed The speed the motors should be set to.
 * @param units Optional units for the speeds.
 * @return Function status
 */
void MotorControl::set_each(int which,
                            float speed_fl, float speed_fr,
                            float speed_bl, float speed_br,
                            char units)
{
    check_which_ok(which);

    ::messages::set_motors msg;


    /* Tell the motors node which motors need to be updated */
    msg.fl_set = msg.fr_set = msg.bl_set = msg.br_set = false;
    if(which & (MOTOR_FL | MOTOR_FL_REV))
    {
        msg.fl_set = true;
        motor_fl_speed = rel_to_abs(speed_fl, units);
    }
    if(which & (MOTOR_FR | MOTOR_FR_REV))
    {
        msg.fr_set = true;
        motor_fr_speed = rel_to_abs(speed_fr, units);
    }
    if(which & (MOTOR_BL | MOTOR_BL_REV))
    {
        msg.bl_set = true;
        motor_bl_speed = rel_to_abs(speed_bl, units);
    }
    if(which & (MOTOR_BR | MOTOR_BR_REV))
    {
        msg.br_set = true;
        motor_br_speed = rel_to_abs(speed_br, units);
    }

    /* Set all the speeds (the booleans in the set_motors message determine
     * which ones will be used) */
    msg.fl_speed = trim_speed("FL", (int) motor_fl_speed);
    msg.fr_speed = trim_speed("FR", (int) motor_fr_speed);
    msg.bl_speed = trim_speed("BL", (int) motor_bl_speed);
    msg.br_speed = trim_speed("BR", (int) motor_br_speed);

    /* Publishes message to set_motors topic */
    set_motors_pub.publish(msg);
    ros::spinOnce();
}

/**
 * Double-checks the which variable to make sure the front and back
 * bits are not both set for a single motor.
 *
 * @param which The which motor specfication to check.
 */
void MotorControl::check_which_ok(int which)
{
    ROS_ERROR_COND( ((which & MOTOR_FL) && (which & MOTOR_FL_REV)),
        "FL Motor set in both directions!");
    ROS_ERROR_COND( ((which & MOTOR_FR) && (which & MOTOR_FR_REV)),
        "FR Motor set in both directions!");
    ROS_ERROR_COND( ((which & MOTOR_BL) && (which & MOTOR_BL_REV)),
        "BL Motor set in both directions!");
    ROS_ERROR_COND( ((which & MOTOR_BR) && (which & MOTOR_BR_REV)),
        "BR Motor set in both directions!");
}

/**
 * Trims an absolute speed to stay within motor maximum range.
 * Uses ROS_WARN to warn the user if a speed has been trimmed.
 *
 * @param which_str A description of which motor, to be used in the warning
 *                  message (for example, "FL")
 * @param speed The requested speed to be set to
 * @return The requested speed, trimmed to stay within limits.
 */
int MotorControl::trim_speed(string which_str, int speed)
{
    int trimmed_speed = speed;
    if (speed > MAXSPEED_ABS)
    {
        trimmed_speed = (int) MAXSPEED_ABS;
        ROS_WARN("Motor (%s) speed trimmed to %d.", which_str.c_str(),
            (int) MAXSPEED_ABS);
    }
    else if (speed < -MAXSPEED_ABS)
    {
        trimmed_speed = (int) -MAXSPEED_ABS;
        ROS_WARN("Motor (%s) speed trimmed to %d.", which_str.c_str(),
            (int) -MAXSPEED_ABS);
    }

    return trimmed_speed;
}
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

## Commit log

2014-10-18 Add Udoo I2C example
2014-11-08 Adding test arduino sketches
2015-02-12 Created readme to keep track of to-do list
2015-02-19 Add electrical
    [ChargingBoard.brd, ChargingBoard.sch, Functional Schematic.sch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]
2015-02-19 Added Odometry

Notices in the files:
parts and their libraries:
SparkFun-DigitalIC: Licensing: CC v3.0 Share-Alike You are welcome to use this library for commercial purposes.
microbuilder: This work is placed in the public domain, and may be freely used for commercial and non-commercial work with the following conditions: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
